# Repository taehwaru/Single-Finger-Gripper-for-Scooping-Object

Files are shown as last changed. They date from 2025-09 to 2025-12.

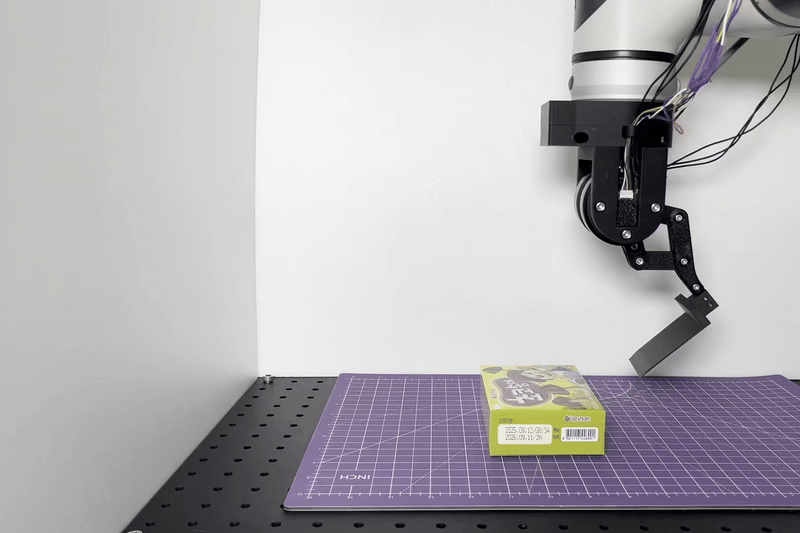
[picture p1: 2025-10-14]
Media/spetula_experiment_cartonbox.gif

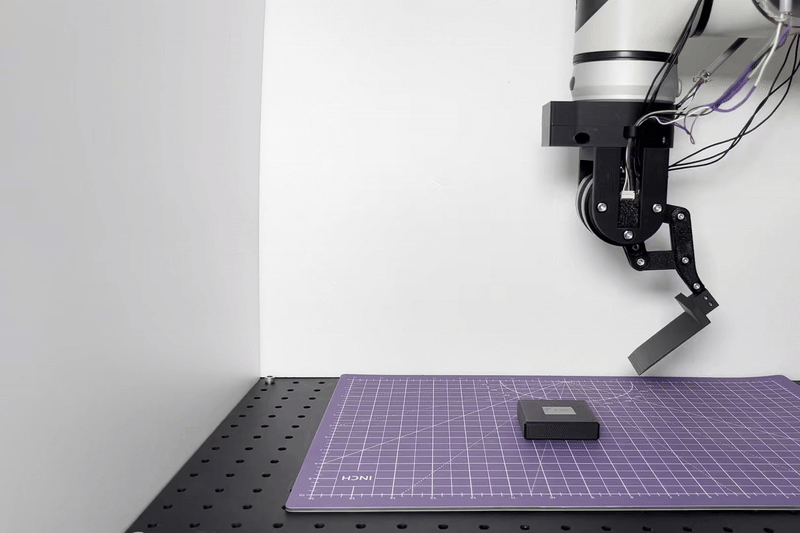
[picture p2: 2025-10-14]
Media/spetula_experiment_50g.gif

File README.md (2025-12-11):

# Direct-Drive Finger for Scooping

We present our **Direct-Drive End-Effector** with Spatulate Fingertip that rapidly inserts beneath an object and scoops it without ejection.
This project is inspired by and extends the work of [Direct-Drive-Gripper-with-Swivel-Fingertips](https://github.com/JS-RML/Direct-Drive-Gripper-with-Swivel-Fingertips).



**Related repos**
* [**High-Speed Scooping (2024)**](https://github.com/JS-RML/Advanced-high-speed-scooping)
* [**Direct-Drive Gripper (2024)**](https://github.com/JS-RML/Direct-Drive-Gripper-with-Swivel-Fingertips)
* [**High-Speed Scooping (2022)**](https://github.com/JS-RML/high_speed_scooping)
* [**Direct-Drive Gripper (2022)**](https://github.com/JS-RML/ddh_hardware)
  
# Table of Contents
- [Parts](#parts)  
  - [Bill of Materials (BOM)](#bill-of-materials-bom)  
      - [Off-the-Shelf Parts](#off-the-shelf-parts)  
      - [3D Printing](#3d-printing)
- [Motors](#motors)
  - [Wiring](#wiring)
    - [Encoder Connection](#encoder-connection)
    - [Motor Connection](#motor-connection)  
  - [Motor Calibration](#motor-calibration)
    - [Calibrate ODrives](#calibrate-odrive)
    - [Calibrate Zero Position](#calibrate-zero-position)
- [Assembly Instructions](#assembly-instructions)  
  - [Direct-Drive Finger Assembly](#direct-drive-finger-assembly) 
  - [Mounting](#mounting)  
    - [Customization](#customization)
- [Software](#software)
  - [Prerequisites](#prerequisites)
    - [Versions](#versions)
    - [Virtual Environment Settings](#virtual-environment-settings)
    - [How to connect Robot Arm and PC](#how-to-connect-robot-arm-and-pc)
  - [Run Finger for Scooping Object](#run-finger-for-scooping-object)
    - [Before running the code](#before-running-the-code)
    - [Let the Finger Gripper for Scooping Object](#let-the-finger-for-scooping-object)
    - [How to customize control parameters](#how-to-customize-control-parameters)
  - [Motor Manipulation](#motor-manipulation)
    - [Example ① : input E](#example---input-e)
    - [Example ② : input T](#example---input-t)
- [Experiments](#experiments)
  - [Experiment Setting](#experiment-setting)
  - [Results](#results)   
    - [Experiment ① : Test Object (10 g)](#experiment---test-object-30-g)  
    -  [Experiment ② : Test Object (30 g)](#experiment---test-object-50-g)  
    - [Experiment ③ : Carton Box (63 g)](#experiment---carton-box-63-g)
    - [Experiment ④ : iphone13 mini (155 g)](#experiment---carton-box-63-g)
- [Contributors](#contributors)
---
# Parts

## Bill of Materials (BOM)
### Off-the-Shelf Parts
- [T-Motor GB54-2](https://store.tmotor.com/goods-445-GB54-2.html) × 2  
- [ODrive S1](https://shop.odriverobotics.com/products/odrive-s1) × 2  
- [AS5048A magnetic encoder + solid magnet](https://ko.aliexpress.com/item/1005001686457940.html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,scm-url:1007.40050.354490.0,pvid:d12cc80d-7f2f-4472-b774-95bc286dbf2c,tpp_buckets:668%232846%238116%232002&pdp_ext_f=%7B%22order%22%3A%225%22%2C%22eval%22%3A%221%22%2C%22sceneId%22%3A%2230050%22%2C%22fromPage%22%3A%22recommend%22%7D&pdp_npi=6%40dis%21KRW%2125633%2117724%21%21%2117.86%2112.35%21%40213ba0c517586181047795086e8a83%2112000017134313267%21rec%21KR%21%21ABXZ%211%210%21n_tag%3A-29910%3Bd%3A7e1d6246%3Bm03_new_user%3A-29895%3BpisId%3A5000000182996635&utparam-url=scene%3ApcDetailTopMoreOtherSeller%7Cquery_from%3A%7Cx_object_id%3A1005001686457940%7C_p_origin_prod%3A#nav-review) × 2
- [Bearings — OD 100 mm / ID 6 mm](https://kr.misumi-ec.com/vona2/detail/221000058378/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) × 3  
- [Wire terminal box](https://freeship.co.kr/goods/content.asp?guid=14063350&cate=&sitecate=mini) × 1  
- [Shielded cable](https://smartstore.naver.com/bantolmarket/products/10633794496) × 1  
- [3-phase cable](https://smartstore.naver.com/shipdiy/products/7890381050?) × 3

### 3D Printing


- **Direct-Drive Finger**
  - [distal_link](https://github.com/taehwaru/Single-Finger-Gripper-for-Scooping-Object/blob/main/STL/Gripper/distal_link.stl) × 2  
  - [distal_tip_cap](https://github.com/taehwaru/Single-Finger-Gripper-for-Scooping-Object/blob/main/STL/Gripper/distal_tip.stl) × 1  
  - [distal_tip](https://github.com/taehwaru/Single-Finger-Gripper-for-Scooping-Object/blob/main/STL/Gripper/distal_tip_cap.stl) × 1  
  - [finger_tip](https://github.com/taehwaru/Single-Finger-Gripper-for-Scooping-Object/blob/main/STL/Gripper/finger_tip.stl) × 2  
  - [motor_shell](https://github.com/taehwaru/Single-Finger-Gripper-for-Scooping-Object/blob/main/STL/Gripper/motor_shell.stl) × 1  
  - [motor_plate](https://github.com/taehwaru/Single-Finger-Gripper-for-Scooping-Object/blob/main/STL/Gripper/motorplate.stl) × 2  
  - [proximal_link](https://github.com/taehwaru/Single-Finger-Gripper-for-Scooping-Object/blob/main/STL/Gripper/proximal_link.stl) × 1
  - [proximal_link_cap](https://github.com/taehwaru/Single-Finger-Gripper-for-Scooping-Object/blob/main/STL/Gripper/proximal_link_cap.stl) × 1
  - [proximal_link_pillar](https://github.com/taehwaru/Single-Finger-Gripper-for-Scooping-Object/blob/main/STL/Gripper/proximal_link_pillar.stl) × 1

- **Mounting**
  - **Robotic Arm** : RB5-850
    - [adapter_plate](https://github.com/taehwaru/Single-Finger-Gripper-for-Scooping-Object/blob/main/STL/Mounting/RB5/adapter_plate.stl) × 1
    - [coupler](https://github.com/taehwaru/Single-Finger-Gripper-for-Scooping-Object/blob/main/STL/Mounting/RB5/coupler.stl)× 1
    - [coupling](https://github.com/taehwaru/Single-Finger-Gripper-for-Scooping-Object/blob/main/STL/Mounting/RB5/coupling.stl)× 1

  - **Drone** : DJI Matrice 400
    - to be added

# Motors
We need two motor subassemblies. Each one can be assembled as follows.


## Wiring
The components should be connected following the diagram below. For power supply, the system supports an input range of DC 12-48V. In our setup, we supplied 24V. The encoder connection will be further elaborated. 


### Encoder Connection
For the encoder connection, we fabricated a cable assembly as shown in the schematic below.

The wires were joined using heat-shrinkable tube (3.0 × 45 mm) instead of soldering.
After aligning the wires inside the tube, apply heat with a heat gun or lighter to shrink the tube and secure the connection.

And Finally, insert the connector into the Odrive S1 as shown in the figure below.



### Motor Connection
Keep the 3-phase connection consistent as shown below.


## Motor Calibration
Each actuator module require calibration before use. This step can not be done after the gripper is assembled, so do not postpone this step.

We explicitly define the direction of the rotor to be the direction the hexagonal logo on the rotor is pointing at, and the zero position of the motor to be when the direction of the motor is pointing at the opposite direction of the power port on the stator.


### Calibrate Odrive
ODrive provides a GUI service for setting up the motordriver. [Odrive GUI](https://gui.odriverobotics.com/inspector) In the configuration tab in this GUI, You can set up the motordriver's configuration. (this step need motor move freely so you don't set like Calibrate Zero Position diagram)
- **Power source**
  - DC bus overvoltage trip level: 26
  - DC bus undervoltage trip level: 22
  - DC max positive current: 'Leave it blank'
  - DC max negative current: -0.5

- **Motor**
  - Type: Gimbal
  - Phase resistance: 2.675
  - Pole pairs: 7
  - KV: 26
  - Current limit: 1
  - Motor calib current: 10
  - Motor calib voltage: 2
  - Lock-in spin current: 10

- **Encoder**
  - Type: SPI (AMS protocol)
  - nCS pin: GPIO 12

- **Control mode**
  - control mode: Position Control
  - Soft velocity limit: 10
  - Hard velocity limit: 13.75
  - Torque limit: 0.192

- **Interface**
  - UART (115200)

### Calibrate Zero Position
Here we calibrate the zero position of the motor. Mount the actuator on the calibration stand and install the calibration arm onto the actuator according to the diagram

Put the motor into zero position as show in the diagram below. Press down the calibration arm to make sure the stand and arm touch tightly.

when your motor is zero position you go to (ODrive0, ODrive1) in the 'inspector' tab of the [Odrive GUI](https://gui.odriverobotics.com/inspector) and set like picture below.(when you finish First step, Second step is you have to click save_configuration variable call button, Refer to [Odrive doucument](https://docs.odriverobotics.com/v/latest/manual/control.html#absolute-encoder-reference-frame_))
guirrreaaaal

# Assembly Instructions

## Direct-Drive Finger Assembly



## Mounting


### Customization
If the default mounting does not work for you, it's very easy to make a custom mount. The end-effector has a 30 mm PCD with 4 ⨉ M4 mounting interface, as shown in the drawing below.



The end-effector is designed to be compatible with **ISO 9409-1-50-4-M6 Flange** (applied Rainbow robotics RB5, Universal Robots UR10e, Universal Robots UR5, etc.). For other robot systems, it would be better to customize the adapter plate and coupling.



# Software
Implemented in **Python 3** on **Ubuntu**. For ODrive basics, see official docs.
## Prerequisites

### Versions
- Ubuntu: `22.04`  
- Python: `3.10.11`  
- ODrive control utility: `0.6.7`

Git clone our software.

```bash 
https://github.com/taehwaru/Single-Finger-Gripper-for-Scooping-Object.git
```

### Virtual Environment Settings
Please open Visual Studio Code terminal and copy and paste the code below to set your virtual environment.  

```bash 
sudo apt-get install python3-venv
python3 -m venv myenv
source myenv/bin/activate
pip install --upgrade odrive
```
if you finish Virtual Environment Settings part, Please refer to [JS-RML, Direct-Drive Gripper with Swivel Fingertips/Software/Getting started](https://github.com/JS-RML/Direct-Drive-Gripper-with-Swivel-Fingertips/tree/main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) to get started.

### How to connect Robot Arm and PC

(1) connect RB5-850 control box and PC with lan cable.

(2) Go to network in Ubuntu settings and enter the information as shown in the picture below.
Screenshot from 2025-11-25 19-53-14

(3) Open the terminal and type ping 192.168.0.10. If it comes out like the picture below, the robot arm and the PC are communicating.
Screenshot from 2025-11-25 20-38-34

## Run Finger for Scooping Object
### Before running the code
Modify GRIPPER/Spatula.py as follows.

(1) Define the variables SN_M1, SN_M2 using the serial numbers of each odrive.
```bash 
SN_M1 = '383F34723539'
SN_M2 = '00E848E15413'
```
(2) Create odrive objects using those SN_M1, SN_M2.
```bash 
odrv0 = odrive.find_any(serial_number=SN_M1)
odrv1 = odrive.find_any(serial_number=SN_M2)
```
(3) Create Actuator objects using the odrive objects above. 
```bash 
MOTOR1 = Actuator(odrv0, 0, 1, 45) 
MOTOR2 = Actuator(odrv1, 0, 1, 45)
```
(4) Select controlSignal in GRIPPER/mainGripper.py. 
```bash 
controlSignal = 'Scoop'
#controlSignal = 'testFinger'
#controlSignal = 'testEdge'
#controlSignal = 'testGetTheta'
#controlSignal = 'testGetEdge'
#controlSignal = 'testGetFingerTip'
#controlSignal = 'testMotionStop'
```
### Let the finger for Scooping Object
Run main.py.
```bash 
python3 main.py
```
### How to customize control parameters
There are a set of control parameters that you can customize for different objects to scoop.
- **initialConfiguration**: Initial configuration
- **goalConfiguration**: Goal configuration
- **pgain**: Motor P-gains after collision.
- **softmax**: Motor current limit
- **torque_soft_max**: Motor positive torque limit(this variable not contain at code so if you want to fix it, you can use odrive gui) 
- **torque_soft_min**: Motor negative torque limit(this variable not contain at code so if you want to fix it, you can use odrive gui) 
- **sensi**: Motor angle Error range

for instance. In the code, the parameters are preset as follows, to scoop a iphone 13 mini (155g).
```bash
#Example code
x0=-40 ,y0=130
shoulder01, shoulder02 = ik_5bar_fingerTip(x0, y0)
initialConfiguration=[shoulder01,shoulder02]

x1=100,y1=10
shoulder11, shoulder12 = ik_5bar_fingerTip(x1, y1)
goalConfiguration=[shoulder11, shoulder12]

pgain=[15,15]
softmax=[4,4]
torque_soft_max=[0.8,0.8]
torque_soft_min=[-0.8,-0.8]
sensi=5
```

## Motor Manipulation
Our end-effector uses a **Coaxial 5-bar (Diamond) Linkage**. The system can be controlled in two modes — either based on the linkage edge point E(xₑ, yₑ) or the fingertip point T(xₜ, yₜ), depending on the desired level of precision. The controller accepts the endpoint position (either E or T) and outputs the two motor commands 𝜃₁ and 𝜃₂.




### Example ① : input E


### Example ② : input T


# Experiments

## Experiment Setting


## Results

| Task Objects | Mass (g) | P-Gain (Stiffness) | Torque Limit (N·m) | Success Rate |
| :---:| :---: | :---: | :---: | :---: |
| 3D Printed | 10-50 | 15 | ±0.4 | 90% (27/30)  |
| Carton Box | 63 | 15 | ±0.4 | 66.6% (20/30)|
| Phone | 155 | 150 | ±0.8 | 60% (20/30)  |

### Experiment ① : Test Object (30 g)


### Experiment ② : Test Object (50 g)


### Experiment ③ : Carton Box (63 g)


### Experiment ④ : iphone13 mini (155 g)


# Contributors
- **Ji-woong Choi**, chjwng@pusan.ac.kr
- **Yong-joo Ryu**, ryj01@pusan.ac.kr
- **Hyun-woo Sung**, zidlt@pusan.ac.kr

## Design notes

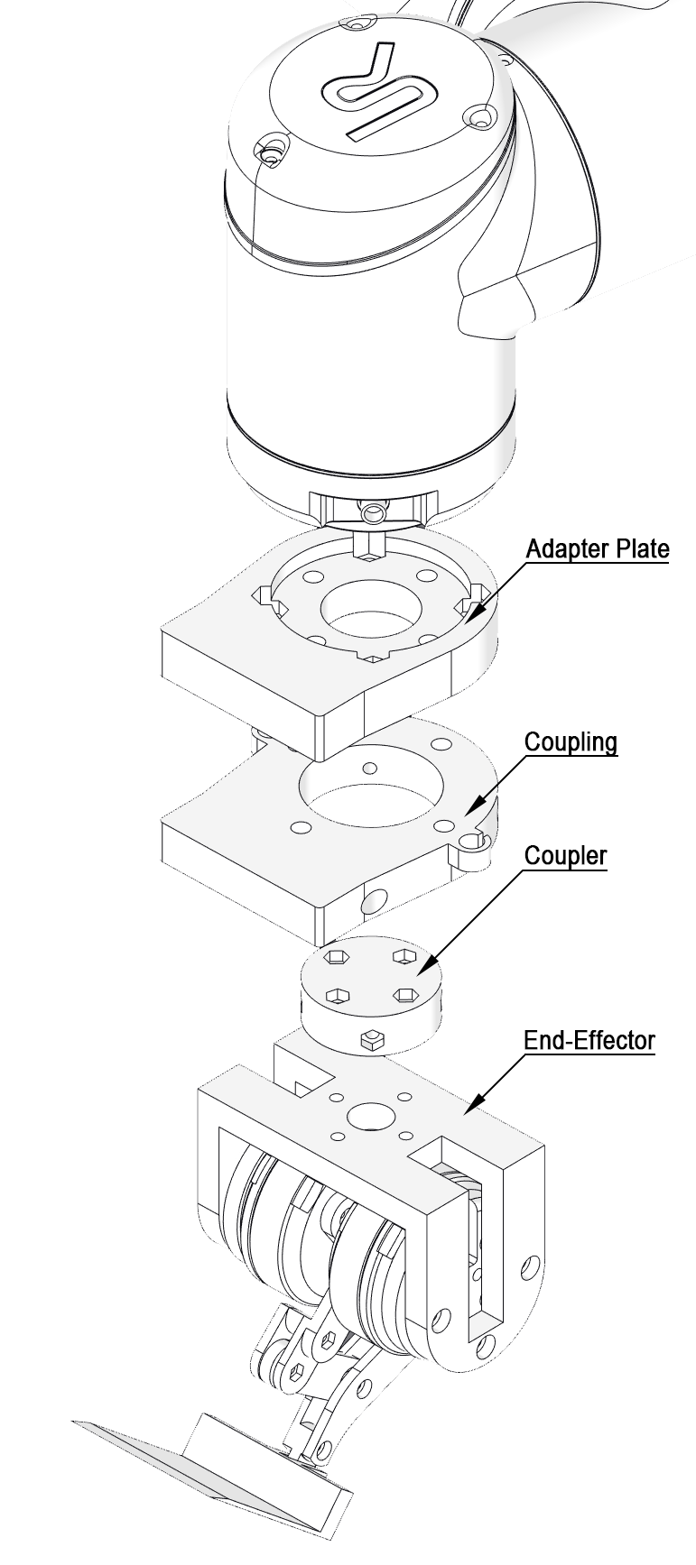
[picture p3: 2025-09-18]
Media/Mounting.png

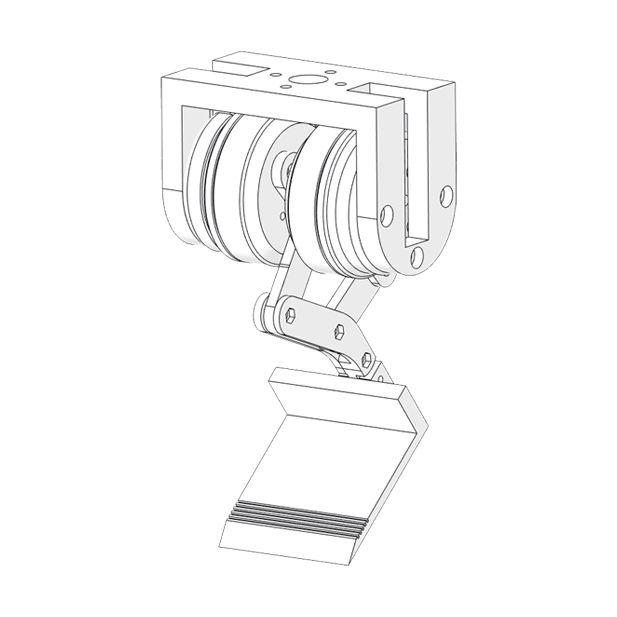
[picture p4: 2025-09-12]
Media/Single-Finger high-speed scooping gripper.png

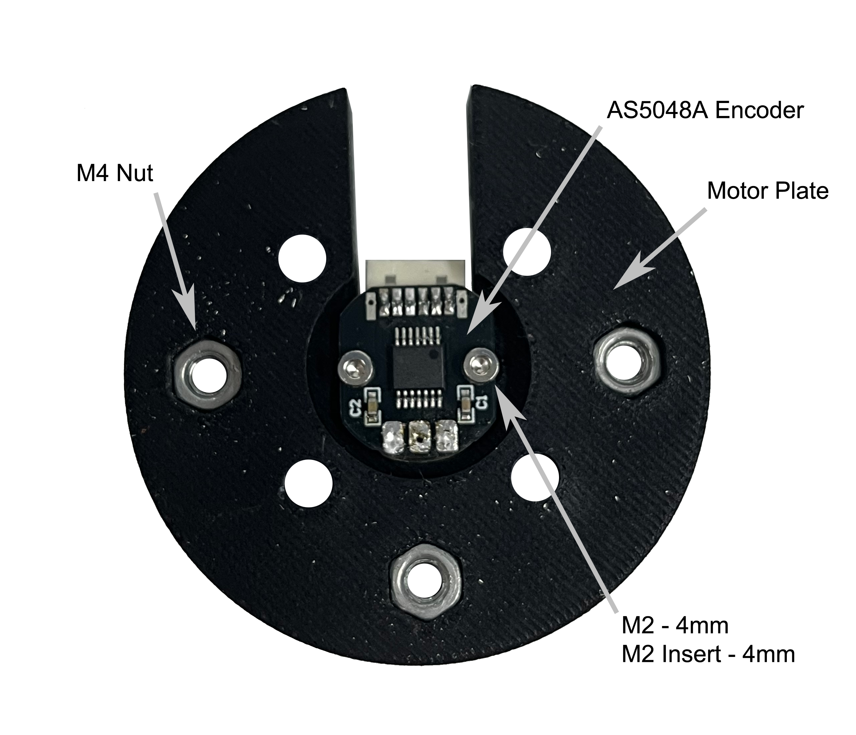
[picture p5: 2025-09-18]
Media/AS5048A Encoder.png

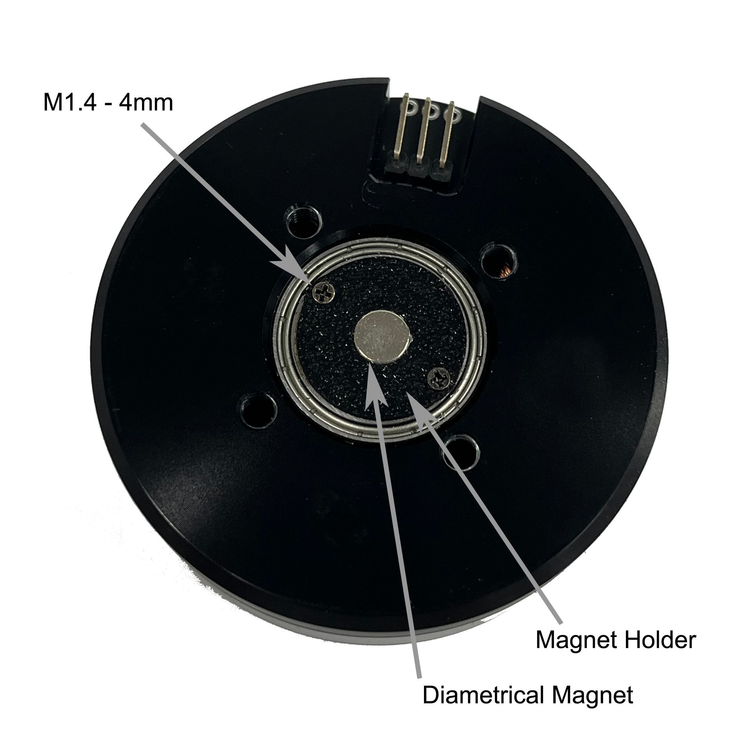
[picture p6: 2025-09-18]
Media/Magnetic Holder.png

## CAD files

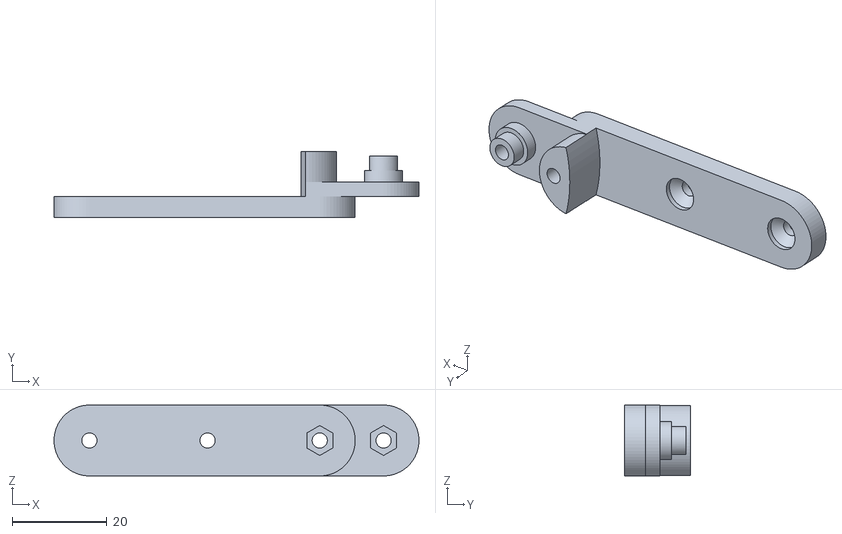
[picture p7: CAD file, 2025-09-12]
STL/Gripper/proximal_link_pillar.stl
77.3 x 14.0 x 15.0

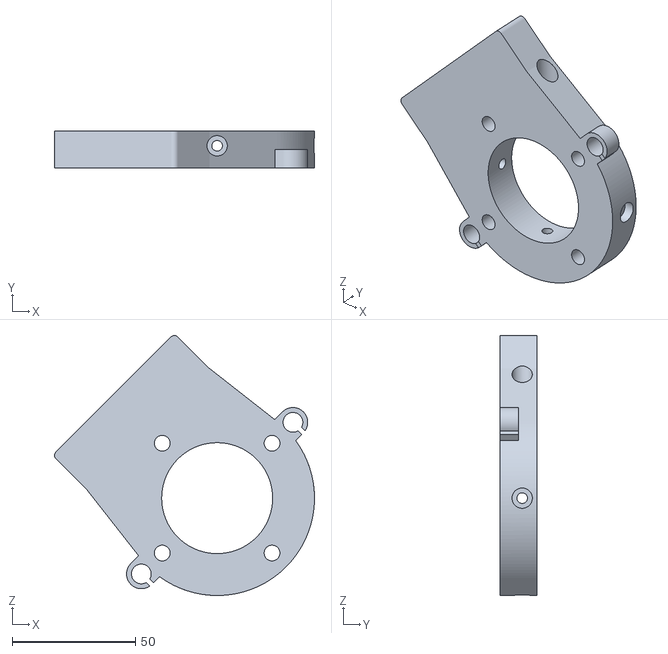
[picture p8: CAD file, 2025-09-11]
STL/Mounting/RB5/coupling.stl
105.5 x 15.0 x 105.5

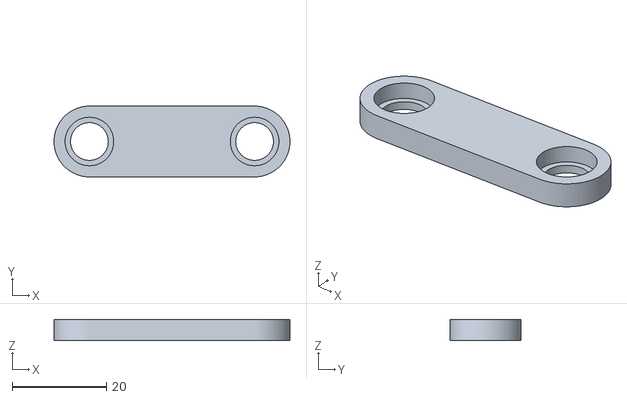
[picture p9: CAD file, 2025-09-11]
STL/Gripper/distal_link.stl
50.0 x 15.0 x 4.50

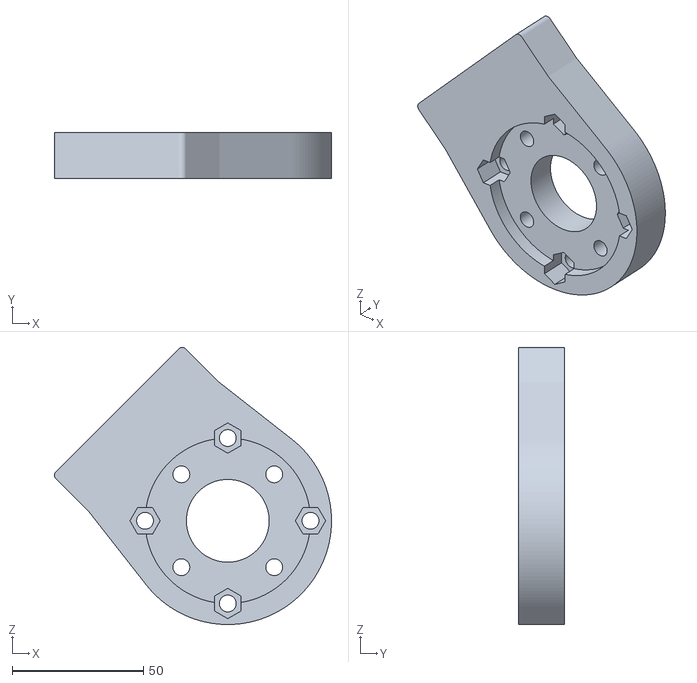
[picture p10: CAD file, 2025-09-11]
STL/Mounting/RB5/adapter_plate.stl
105.5 x 17.5 x 105.5

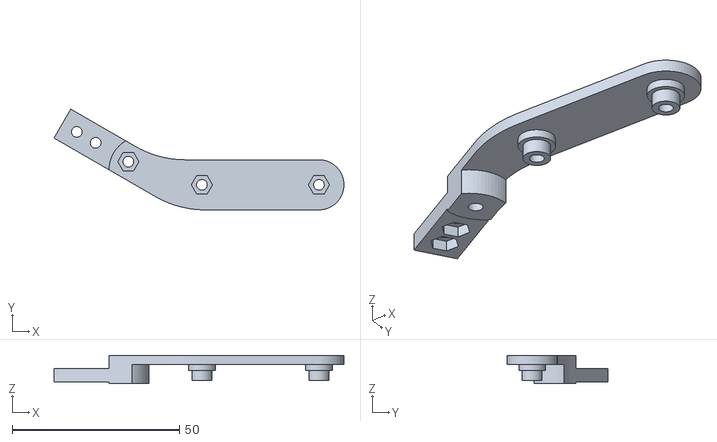
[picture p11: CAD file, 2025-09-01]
STL/Gripper/distal_tip.stl
86.7 x 30.2 x 8.50

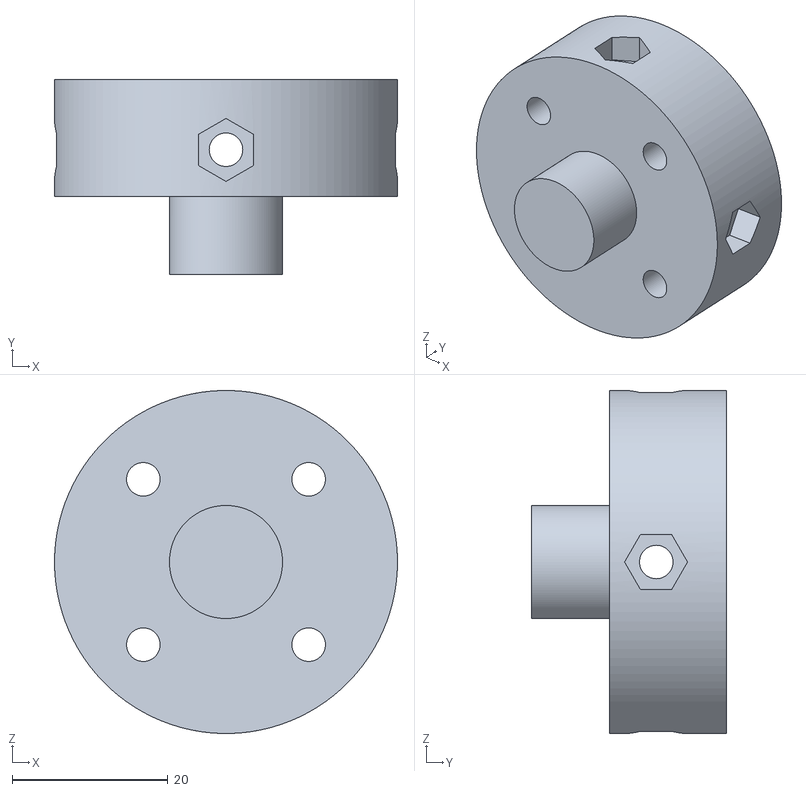
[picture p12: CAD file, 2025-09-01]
STL/Mounting/RB5/coupler.stl
44.0 x 25.0 x 44.0

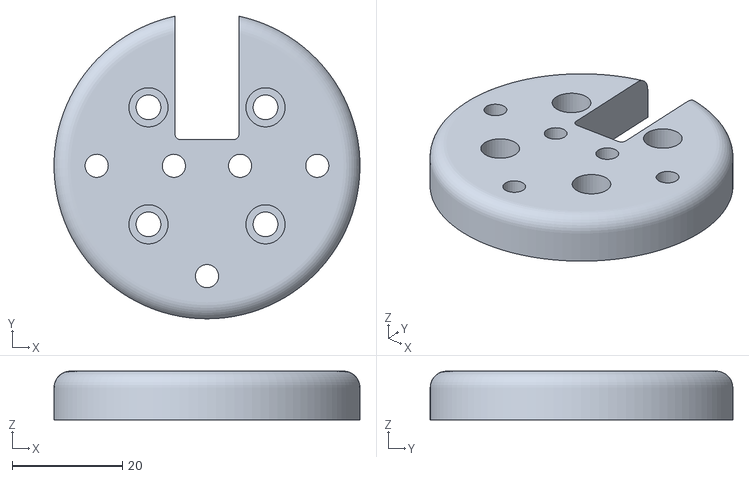
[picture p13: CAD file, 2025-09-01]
STL/Gripper/motorplate.stl
55.5 x 54.9 x 8.85

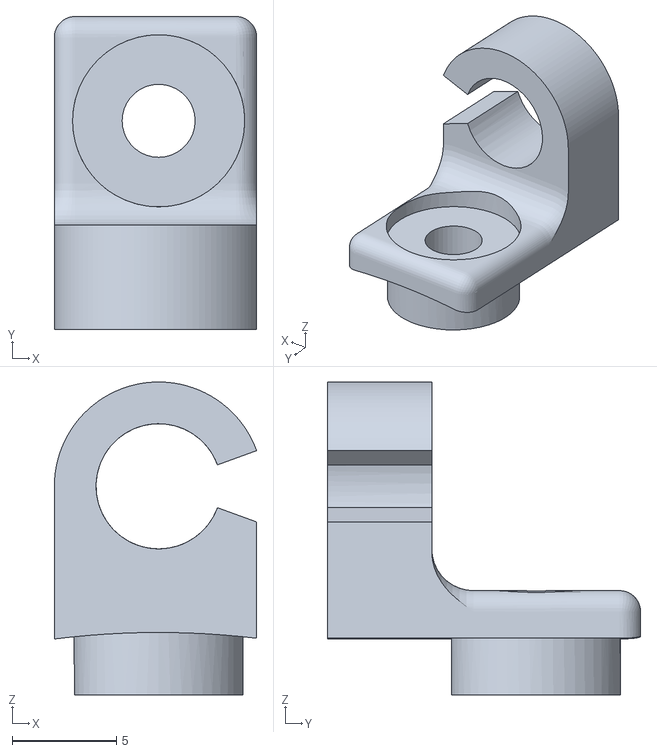
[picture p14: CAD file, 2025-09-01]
STL/Mounting/RB5/wire_holder.stl
9.70 x 15.0 x 15.0

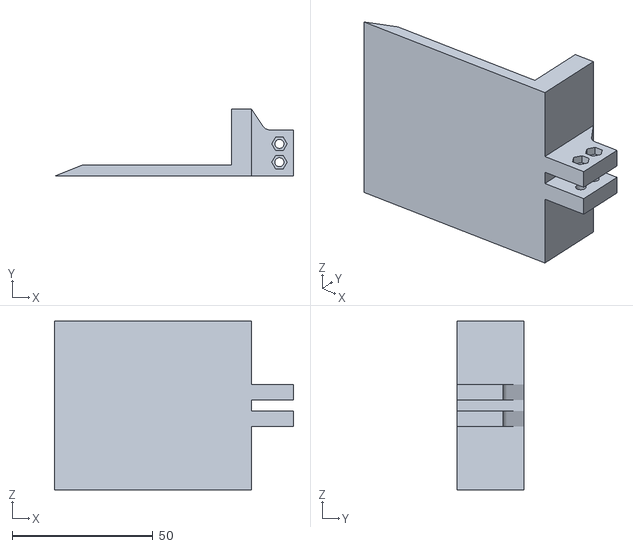
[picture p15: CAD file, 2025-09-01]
STL/Gripper/finger_tip.stl
85.0 x 24.0 x 60.0

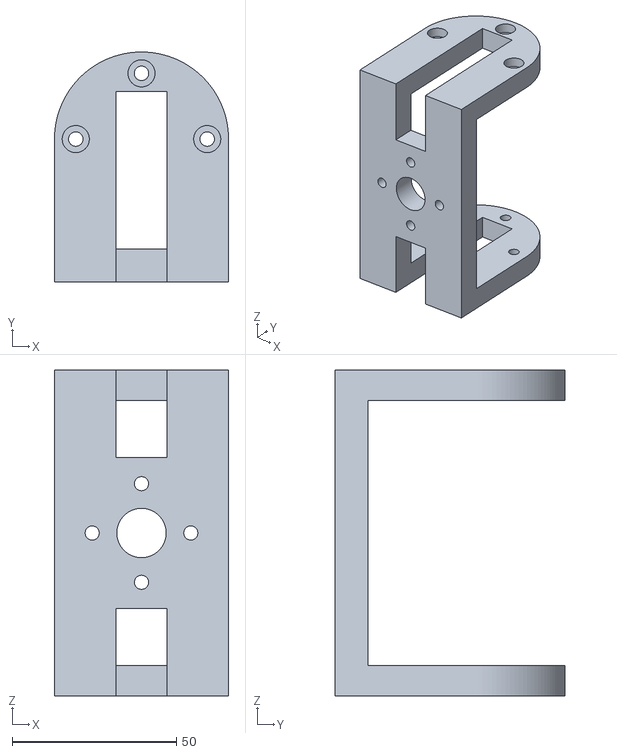
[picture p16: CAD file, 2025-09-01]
STL/Gripper/motor_shell.stl
53.0 x 70.0 x 99.2

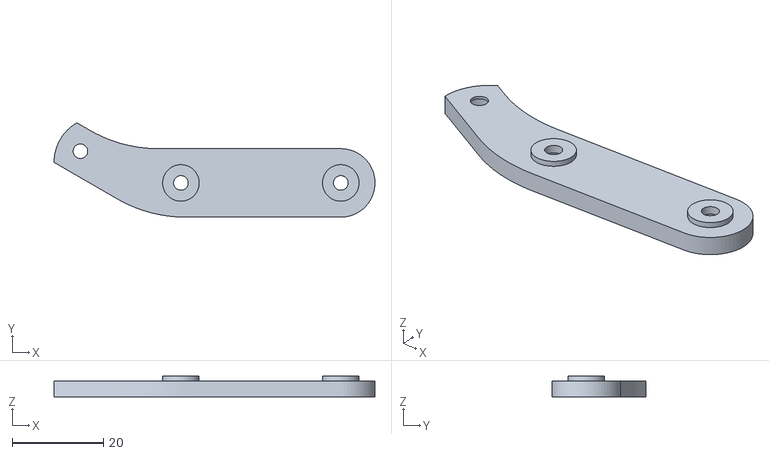
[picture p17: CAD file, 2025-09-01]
STL/Gripper/distal_tip_cap.stl
70.3 x 20.7 x 4.50

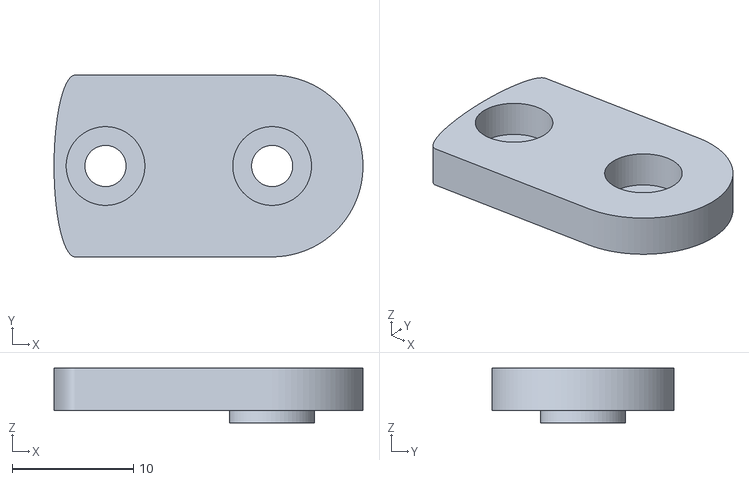
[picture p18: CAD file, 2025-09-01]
STL/Gripper/proximal_link_cap.stl
25.5 x 15.0 x 4.50

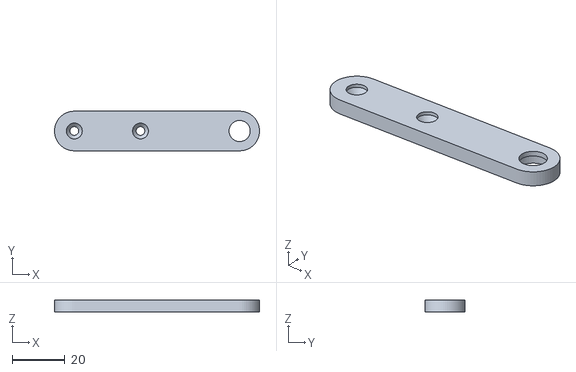
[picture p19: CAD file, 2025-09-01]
STL/Gripper/proximal_link.stl
77.5 x 15.0 x 4.50

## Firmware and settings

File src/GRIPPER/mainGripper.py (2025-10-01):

import sys
import os
current_dir_gripper = os.path.dirname(os.path.abspath(__file__)) # 예를들어 부모 디렉토리를 만든다면 parent_dir = os.path.join(current_dir, '..') 이렇게도 가능
sys.path.append(current_dir_gripper)
#from GRIPPER import Gripper
from GRIPPER import Spatula
import TestMotion

######## select control signal ########
#controlSignal = 'testFinger'
#controlSignal = 'testEdge'
#controlSignal = 'Scoop'
#controlSignal = 'testGetTheta'
controlSignal = 'testGetEdge'
#controlSignal = 'testGetFingerTip'
#controlSignal = 'testMotionStop'
######################################

def switchCase(case):
    if case == 'testFinger' :
        TestMotion.Test_fingerTip()

    elif case == 'testEdge' :
        TestMotion.Test_linkageEdge()

    elif case == 'Scoop' :
        TestMotion.Scoop()

    elif case == 'testGetTheta' :
        TestMotion.TestGetTheta()

    elif case == 'testGetEdge' :
        TestMotion.TestGetEdge()

    elif case == 'testGetFingerTip' :
        TestMotion.TestGetFingerTip()        

    elif case == 'testMotionStop' :
        TestMotion.TestMotionStop()    

    else:
        print("Check the controlSignal")

# Gripper main is started
def mainGripper():
    switchCase(controlSignal)

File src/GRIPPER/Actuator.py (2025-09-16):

from odrive.enums import *

class Actuator(object):

    def __init__(self, odrv, encoder_offset, direction, link_offset):
        self.odrv = odrv
        self.axis = odrv.axis0
        self.encoder_offset = encoder_offset
        self.direction = direction
        self.link_offset = link_offset
        self.setPointOffset = encoder_offset

    
    @property
    def encoder(self):
        posEstimate = self.odrv.axis0.pos_estimate
        calibratedEncoder = posEstimate
        return calibratedEncoder

    @property
    def motor_pos(self):
        tempEncoderValue = self.odrv.axis0.pos_estimate
        return 360 * (tempEncoderValue - self.setPointOffset)
        
   
    @motor_pos.setter
    def motor_pos(self, desiredMotorPosition):
        desiredSetPoint = desiredMotorPosition / 360 + self.setPointOffset
        self.axis.controller.input_pos = desiredSetPoint

    @property
    def theta(self):
        return self.motor_pos + self.link_offset

    @theta.setter
    def theta(self, setpoint):
        self.motor_pos = setpoint - self.link_offset

    @property
    def armed(self):
        return self.axis.current_state is AxisState.CLOSED_LOOP_CONTROL

    @armed.setter
    def armed(self, val):
        if val:  # arm
            self.axis.controller.config.input_mode = InputMode.PASSTHROUGH
            self.axis.requested_state = AxisState.CLOSED_LOOP_CONTROL
        else:  # disarm
            self.axis.requested_state = AxisState.IDLE

    @property
    def stiffness(self):
        return self.axis.controller.config.pos_gain

    @stiffness.setter
    def stiffness(self, val):
        self.axis.controller.config.pos_gain = val
    @property
    def current_soft_max(self):
        return self.axis.config.motor.current_soft_max
    
    @current_soft_max.setter
    def current_soft_max(self,val):
        self.axis.config.motor.current_soft_max=val

    @property
    def torque_soft_max(self):
        return self.axis.config.torque_soft_max
        
    @torque_soft_max.setter
    def torque_soft_max(self,val):
        self.axis.config.torque_soft_max=val


    @property
    def motor_vel(self):
        return self.axis.controller.input_vel

    @motor_vel.setter
    def motor_vel(self, val):
        self.axis.controller.input_vel = val

    @property
    def vel_gain(self):
        return self.axis.controller.config.vel_gain

    @vel_gain.setter
    def vel_gain(self, val):
        self.axis.controller.config.vel_gain = val

    @property
    def bandwidth(self):
        return self.axis.controller.config.input_filter_bandwidth

    @bandwidth.setter
    def bandwidth(self, val):
        self.axis.controller.config.input_filter_bandwidth = val

    def iBusValue(self):
        return self.odrv.ibus

    def clearErrors(self):
        self.odrv.clear_errors()

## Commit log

2025-09-12 Rename One finger high-speed scooping gripper.png to Single-Finger high-speed scooping gripper.png
2025-09-12 Rename SSingle-Finger high-speed scooping gripper.png to Single-Finger high-speed scooping gripper.png
2025-09-16 Create Gripper
2025-09-29 README.md 업데이트
2025-11-24 Add motor calibration instructions to README
    Added sections for motor calibration and ODrive setup.
2025-11-27 Revise README for Direct-Drive Finger project
    Updated project title and descriptions for clarity. Changed references from 'Single-Finger Gripper' to 'Direct-Drive Finger' and adjusted related text accordingly.
2025-11-27 Update motor image in README
2025-12-01 Revise mounting and customization descriptions in README
    Updated mounting and customization sections to clarify terminology and improve readability.
2025-12-01 Update README with new mounting image
    Added an additional image for the mounting section.
